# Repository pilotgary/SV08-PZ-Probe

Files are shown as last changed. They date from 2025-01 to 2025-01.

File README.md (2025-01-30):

# SV08-PZ-Probe
E3D Revo PZ-Probe for the Sovol SV08

## Project Aims
1. To swap the supplied hot end and Z probe for the E3D Revo PZ-Probe.
2. To use as many of the existing parts as possible.
3. To work with the Sovol branch of Klipper.
4. 3D printed parts should not require support.

> [!IMPORTANT]
> Full details of the PZ probe can be found on the E3D support page at https://e3d-online.com/pages/e3d-support-pz-probe
> Please read these instruction thoroughly before proceeding. 

## New 3D printed parts 
The new 3d printed parts can be found in the STEP directory.  As most modern slicers can open STEP files directly this is the preferred format for this project.  Premade 3MF files for the Bambu Labs A1 mini and STL files are available in the relevant folders.

The parts should be orientated correctly on import as shown below. All parts have been designed so that support is not required, provided your printer can cope with small bridges.

### Print Orientation
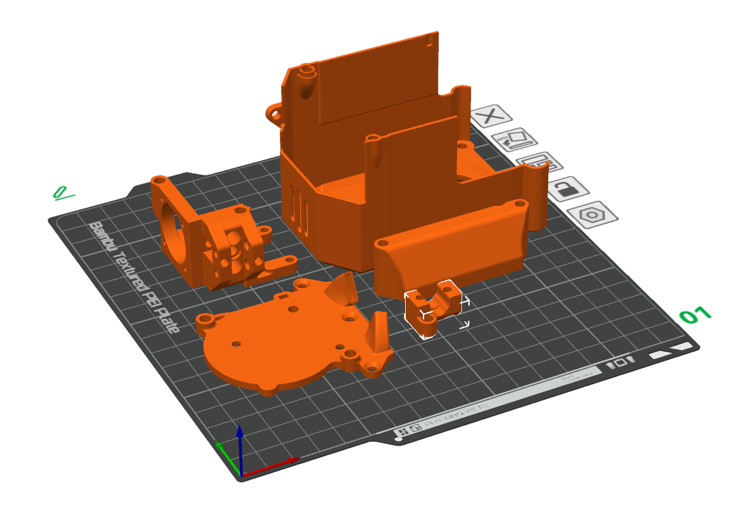
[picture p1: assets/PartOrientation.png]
Part orientation


The prototype was printed in PETG on a Bambu Labs A1 mini, 0.16mm layer height, 3 wall loops, 100% infill.  If your Sovol SV08 has an enclosure or you plan on printing high temperature filamanets, ASA or ABS would be preferred.

## Printed Part Preparation

### Heat set inserts

The parts are designed around M3 x 6mm unflanged inserts, except for the upper two on the main mount, that should be M3 x 5mm.  If preferred, 5mm long inserts can be used in all locations. Alternatively, 6mm inserts can be used everywhere, if you don't mind them sticking out a little from the main mount.  

All inserts should sit level or below the face of insertion.  Any plastic the bulges up should be removed, so that parts fir together without gaps.

#### Main Mount

The main mount upper inserts need to be aligned with the inside of the mounting slot for maximum strength and ease of assembly.  See the image below.

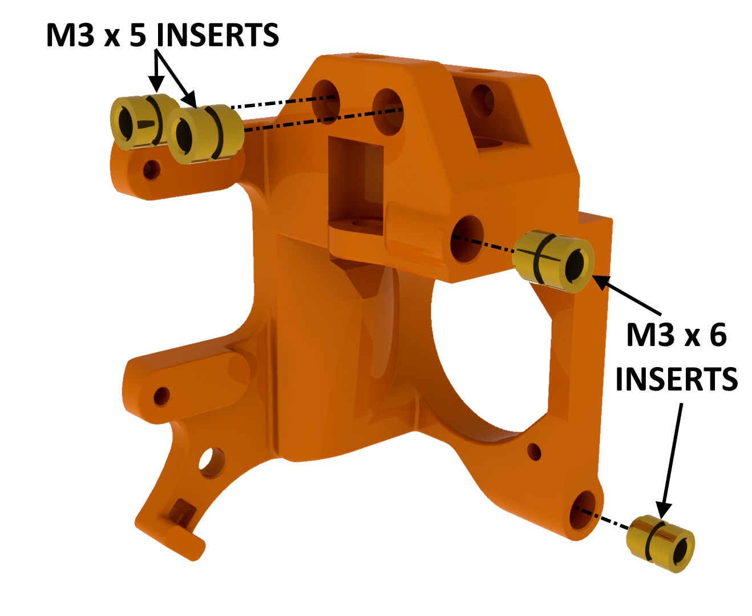
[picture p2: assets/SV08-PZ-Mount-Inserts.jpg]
SV08-PZ-Mount-Inserts
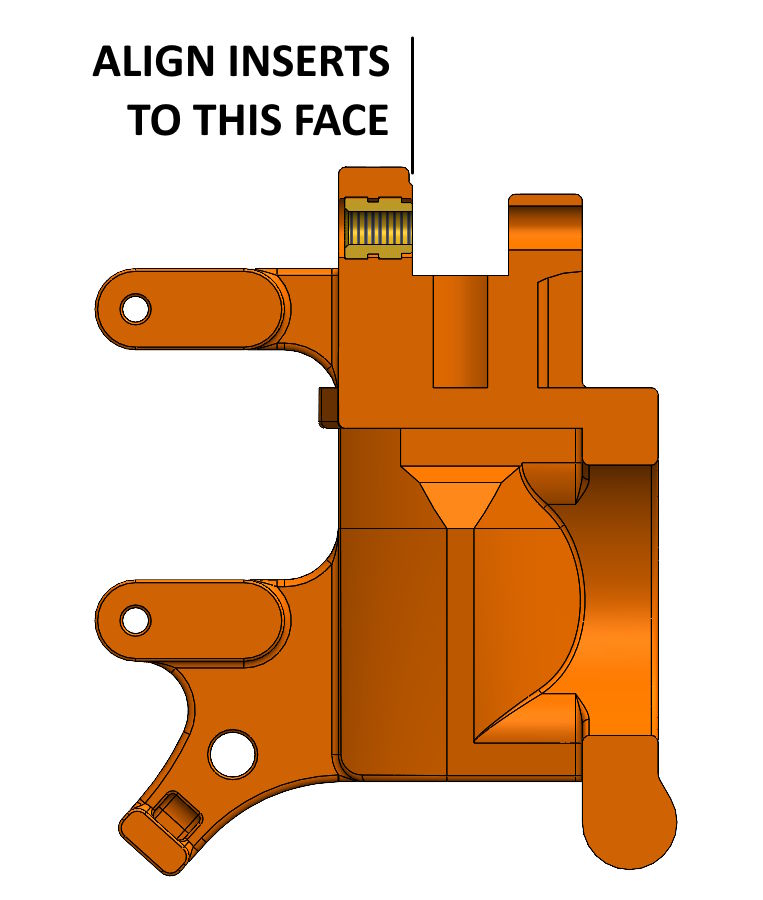
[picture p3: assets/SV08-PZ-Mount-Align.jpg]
SV08-PZ-Mount-Align
 

#### Fan mount with nozzles

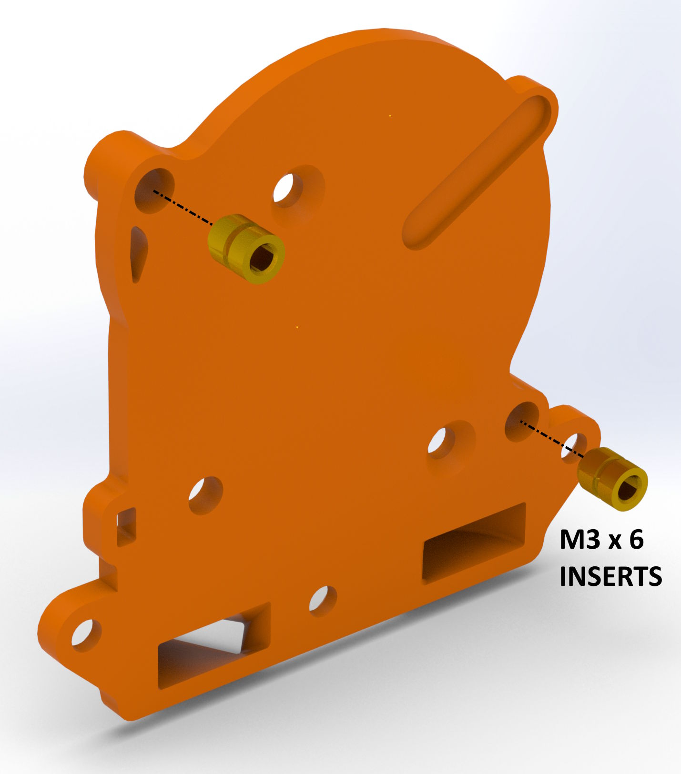
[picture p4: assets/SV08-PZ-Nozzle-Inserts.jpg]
SV08-PZ-Nozzle-Inserts


#### Fan mount interface

Make sure the inserts sit below the mating face and remove any plastic preventing the mating face from sitting flat, to ensure an airtight seal with the nozzles.

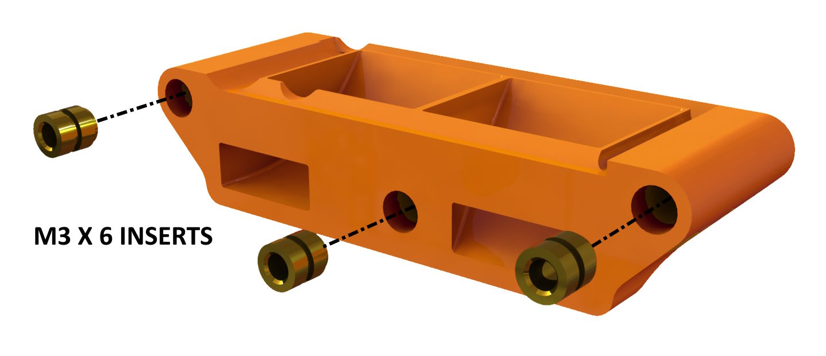
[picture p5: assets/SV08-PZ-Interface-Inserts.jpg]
SV08-PZ-Interface-Inserts


#### Cable clamp

The cable clamp uses a sacrificial layer to support the counterbored screw holes.  This will need to be drilled through.

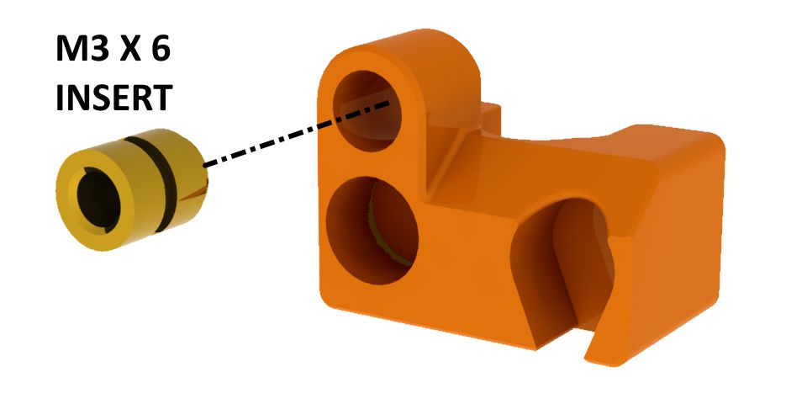
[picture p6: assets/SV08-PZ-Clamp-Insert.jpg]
SV08-PZ-Clamp-Insert
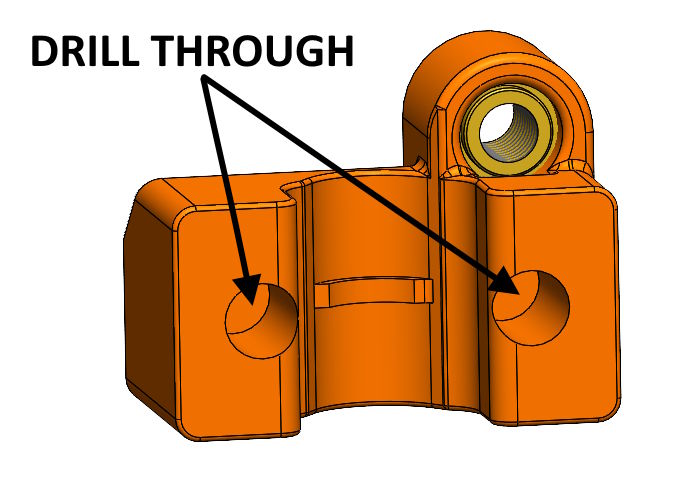
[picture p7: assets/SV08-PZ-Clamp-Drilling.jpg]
SV08-PZ-Clamp-Drilling
  

### Magnets

This design uses 4mm diameter x 3mm long neodium magnets.  I used these ones https://www.amazon.co.uk/dp/B0C81HTXTV

It is important to ensure that the magnets are inserted the correct way round.  The easiest way to ensure this is to snap the magnet to an already mounted one on the tool head and mark the non-contact face with a permanent marker.  The marked face goes at the bottom of the hole on the cover. With care, for some of the magnets, it is possible to push the mounting hole over the magnet while it is snapped in place.

#### Cover

Try to keep all the magnets orientated the same way.

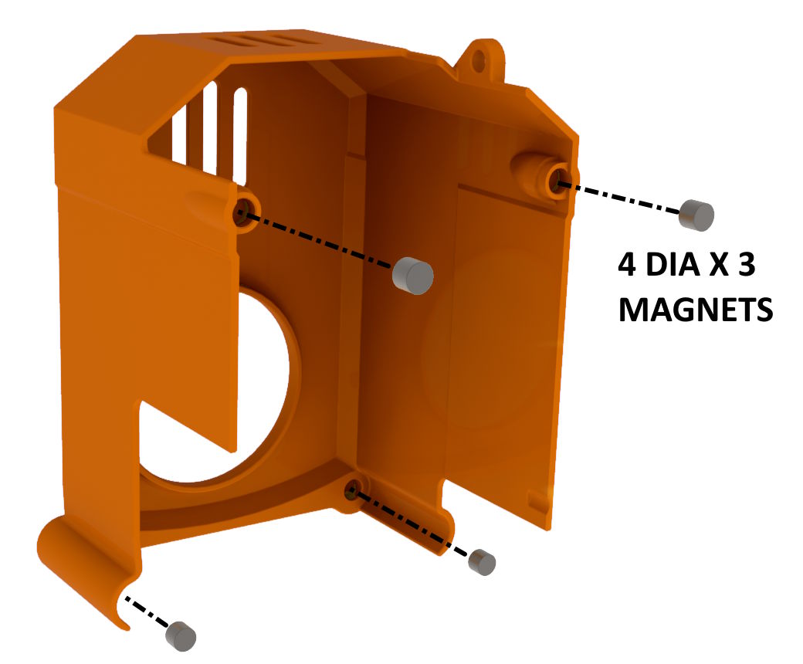
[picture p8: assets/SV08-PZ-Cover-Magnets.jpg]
SV08-PZ-Cover-Magnets


#### Fan mount interface

Snap a magnets to each of the lower pair in the cover.  Slide the interface into the cover and press the two parts together.  Once the magnets are partially seated in the fan interface it can be removed and pressed against a flat surface to fully seat them.

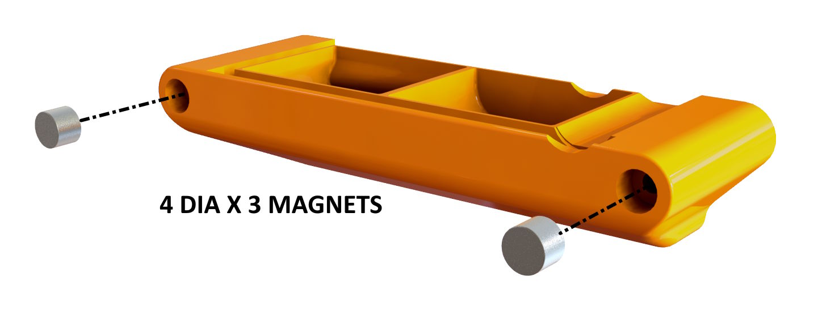
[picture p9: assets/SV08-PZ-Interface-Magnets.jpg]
SV08-PZ-Interface-Magnets


## Stripping the exiting toolhead

1. Home the printer and raise the gantry above 250mm for ease of access with the head front and centre.
   
2. Disconnect the large fan and remove it from the cover.

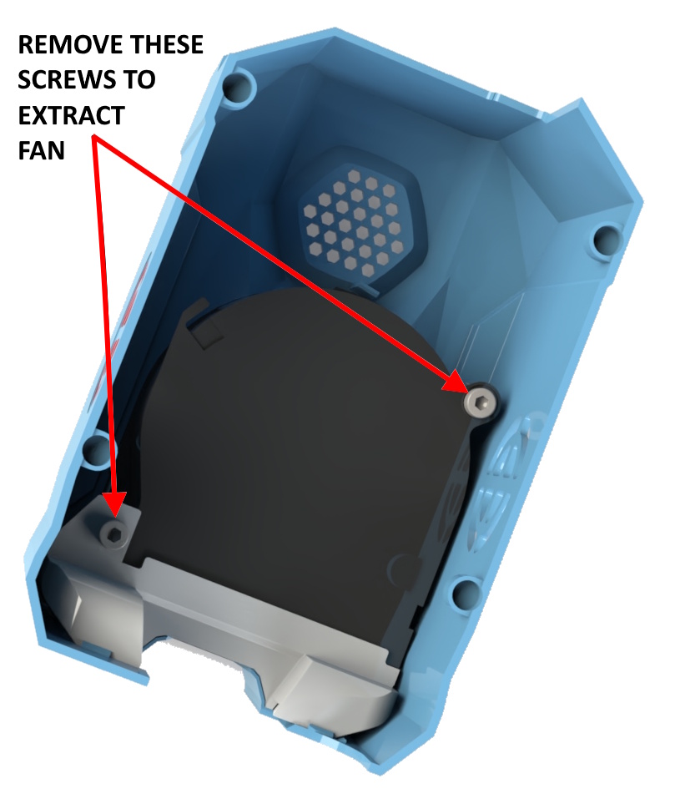
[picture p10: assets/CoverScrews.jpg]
Cover screws
    
    
3. Remove the standard nozzle and heatsink assembly. Clicking on the image below will take you to the relevant Sovol video:
   
   Nozzle change video (http://www.youtube.com/watch?v=bAOVA6bL-Jw)
   
4. Remove the small fan from the heatsink.  Keep the screws.
   
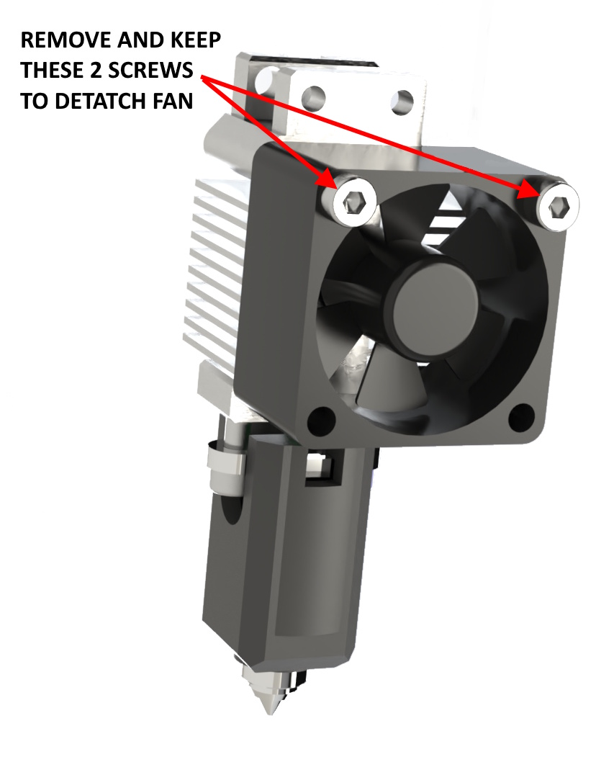
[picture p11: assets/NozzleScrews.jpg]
Nozzle screws
   
   
5. Unscrew the Z-Probe and disconnect the cable. Remove the cable clamp. You can optionally disconnect the power and usb connections for clearer access.
   
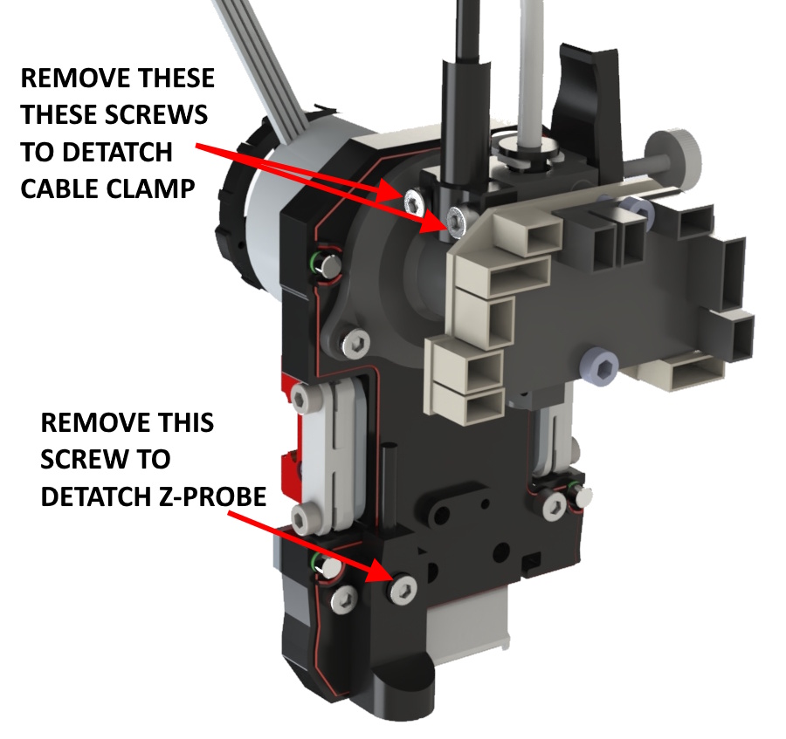
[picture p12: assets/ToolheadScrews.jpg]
Toolhead screws
   

## PZ-Probe Assembly

Align the coldside on the mount so that the cable points away from the fan ring and assemble using M3x6 buttonhead screws.  The two side screws are placed in their cut-outs and the hex driver engages in their heads through the holes in the top.

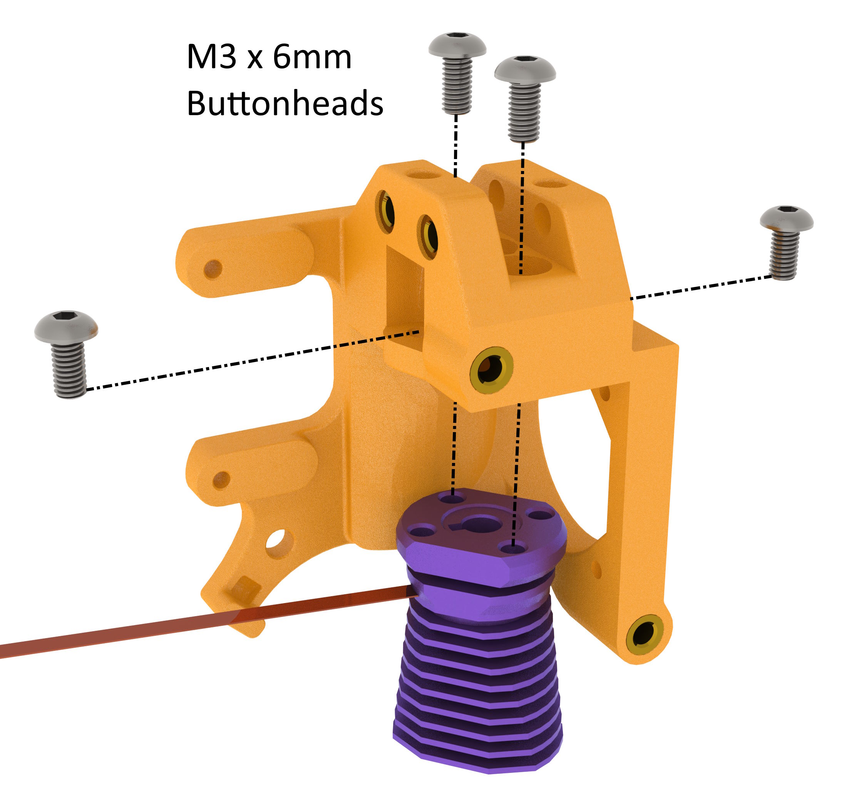
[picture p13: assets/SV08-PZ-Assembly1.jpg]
SV08-PZ-Assembly1
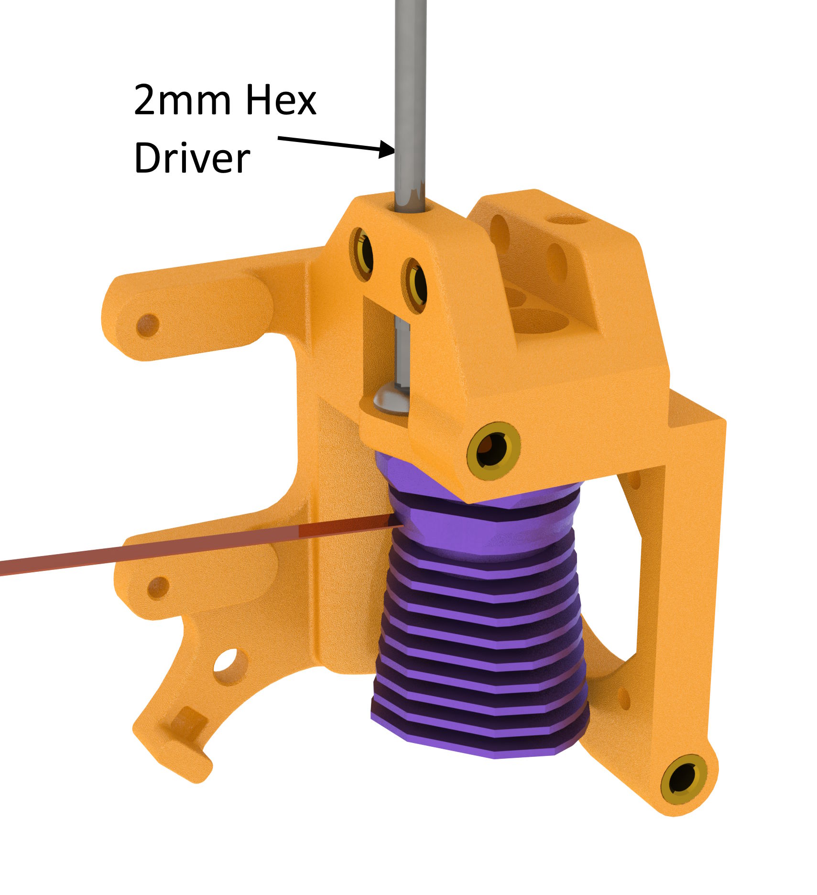
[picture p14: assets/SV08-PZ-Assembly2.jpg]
SV08-PZ-Assembly2
 

Mount the PZ-probe board in place using the M2 capheads supplied with the board.  These screws will cut their own threads in the mount.

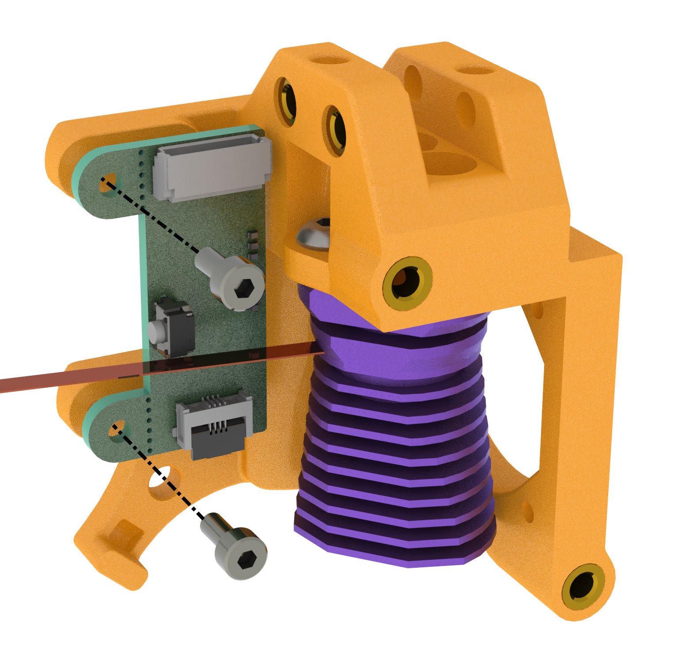
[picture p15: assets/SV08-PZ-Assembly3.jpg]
SV08-PZ-Assembly3


Loop the ribbon cable around and connect tto the pz-probe board.  Use a small zip tie to hold it in place.

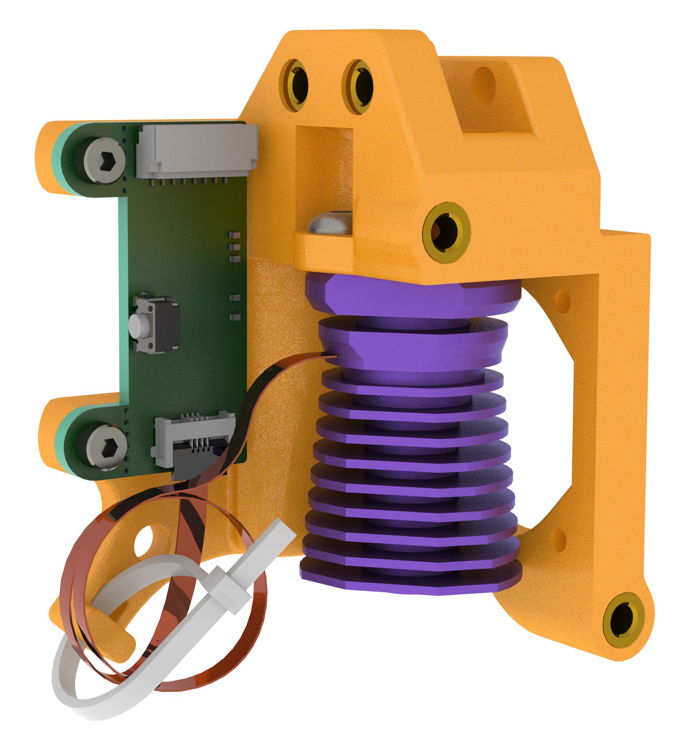
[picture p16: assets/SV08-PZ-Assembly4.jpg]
SV08-PZ-Assembly4
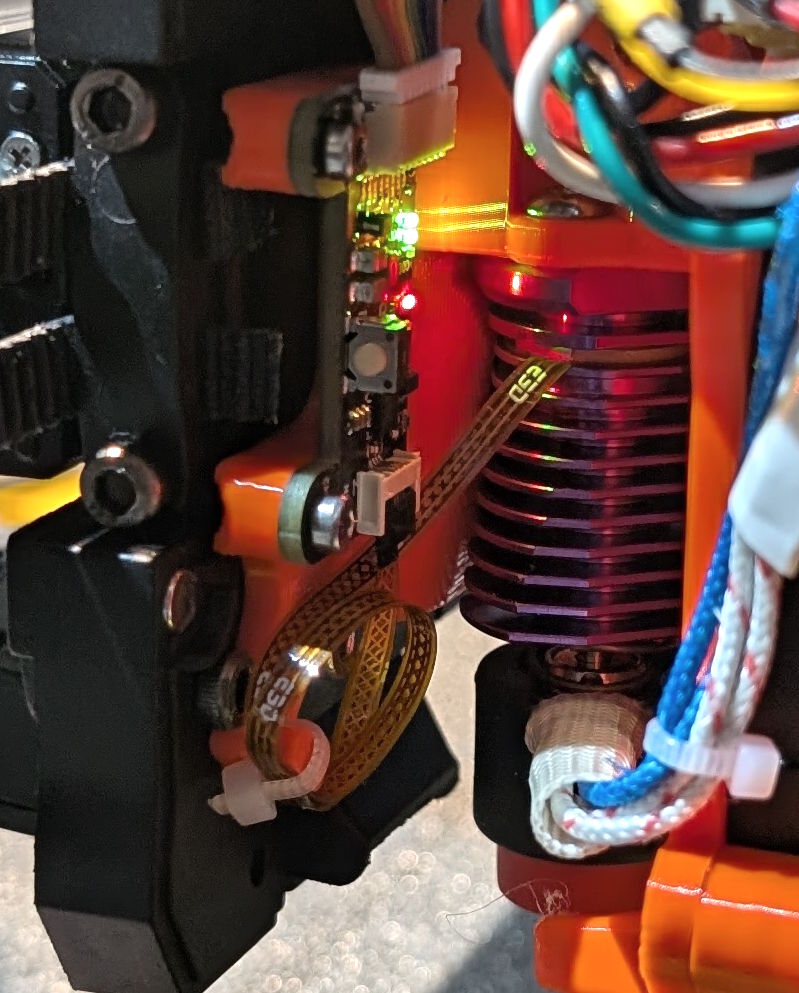
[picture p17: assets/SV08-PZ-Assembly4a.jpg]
SV08-PZ-Assembly4a
 

Using the original 2 screws attach the cold end cooling fan.  4 holes are available but only two are needed.  The screws will cut their own thead.

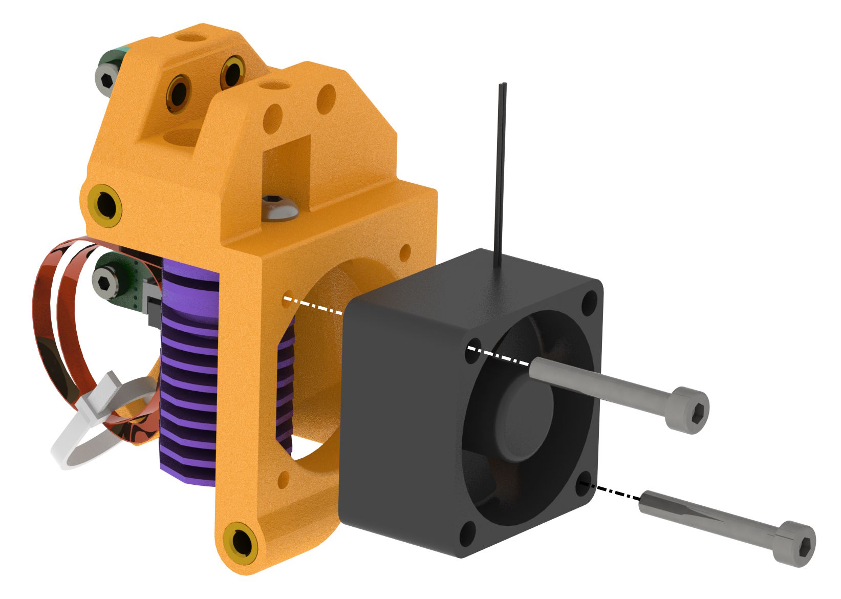
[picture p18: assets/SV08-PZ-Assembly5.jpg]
SV08-PZ-Assembly5


The PZ-Probe comes with a short length of bowden tube. Cut this to 33.5mm, and insert through the mount until it bottoms in the heatsink.  

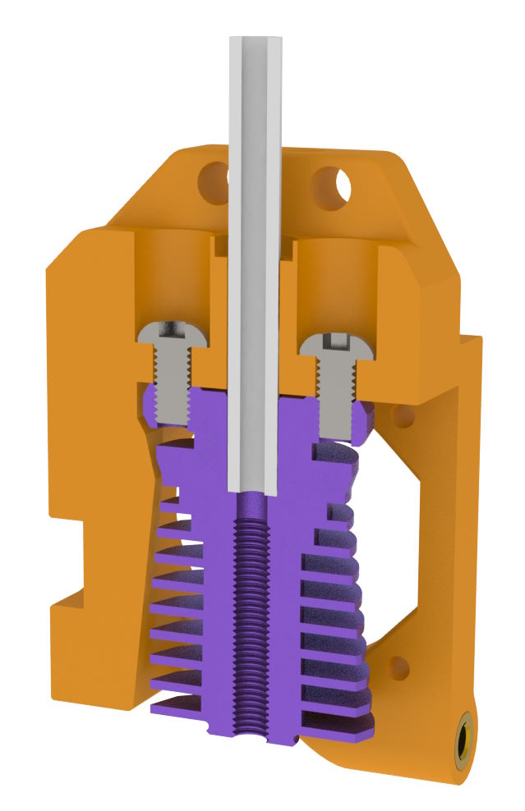
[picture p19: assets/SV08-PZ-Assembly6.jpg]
SV08-PZ-Assembly6


Insert the bowden tube into the toolhead as shown below and push up.  The mount will snap over the original heatsink mount. If the mount doesn't seat completely, trim a small amount off of the bowden tube and try again. 

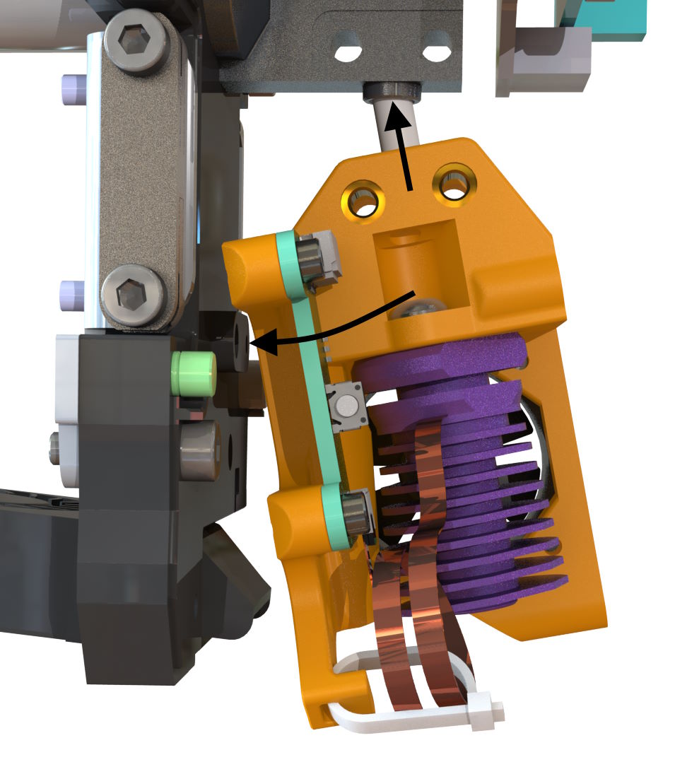
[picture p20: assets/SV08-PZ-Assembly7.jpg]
SV08-PZ-Assembly7
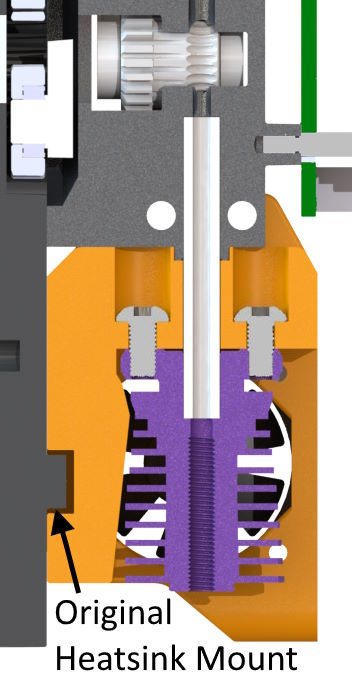
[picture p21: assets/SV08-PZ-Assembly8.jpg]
SV08-PZ-Assembly8
 

Use two M3x20 and one M3x8 screws to secure the mount.  The screws enter from the opposite side compared to the original heatsink.

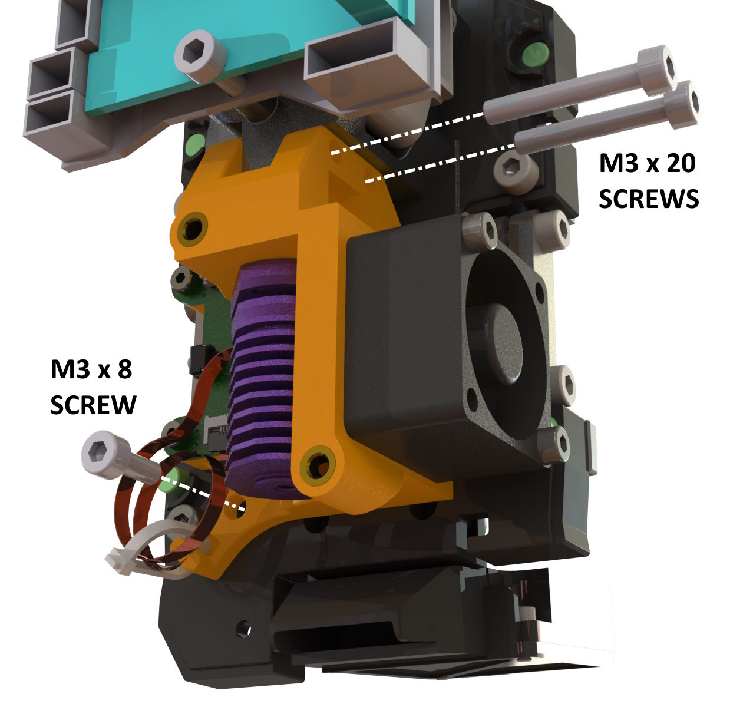
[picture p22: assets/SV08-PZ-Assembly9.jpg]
SV08-PZ-Assembly9


Combine the part cooling fan interface and nozzle items together with three M3x8 countersunk screws

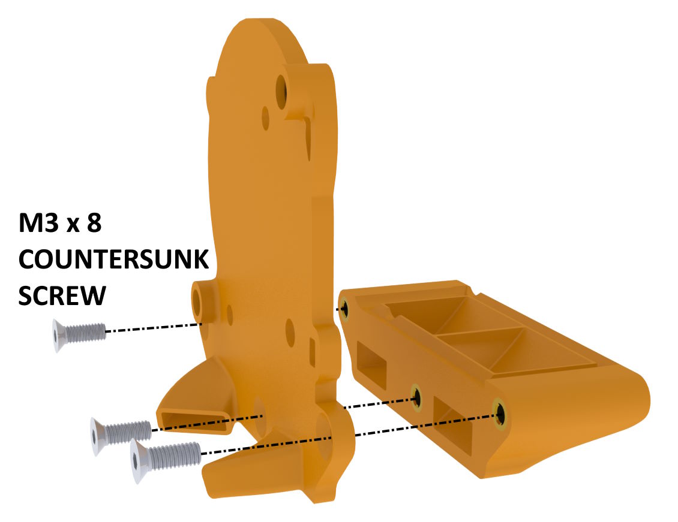
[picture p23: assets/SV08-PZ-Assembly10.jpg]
SV08-PZ-Assembly10


Fix this to the main mount with two M3x8 countersunk screws.  The next stage is the wiring and it's handy to have the fan mount in place to determine the wire lengths.

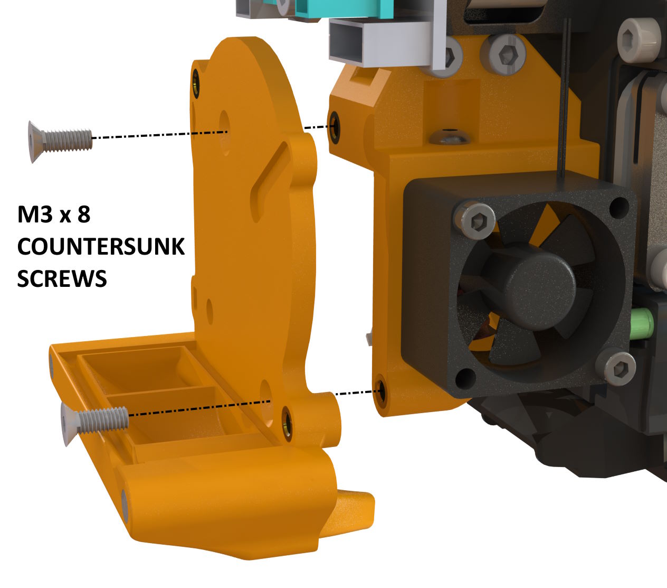
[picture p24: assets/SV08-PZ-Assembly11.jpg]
SV08-PZ-Assembly11


Slot the 5020 fan into the interface and fix with M3x25 screws and washers.  The washers help protect the fan case from splitting from the screw heads. 

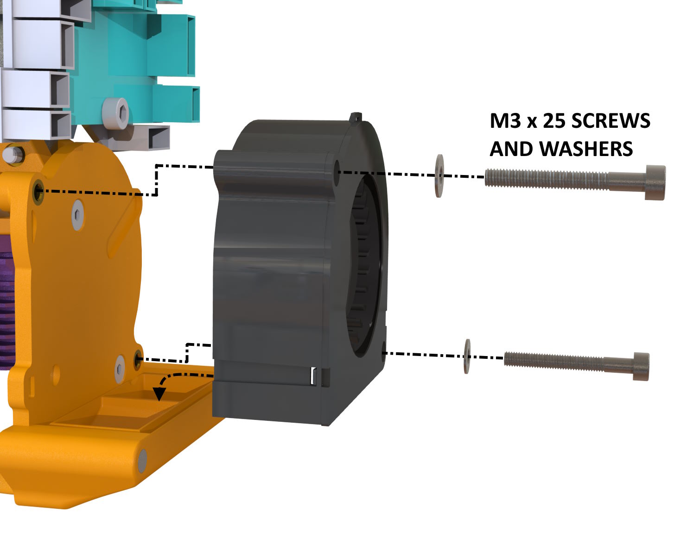
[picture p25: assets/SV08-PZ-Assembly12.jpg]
SV08-PZ-Assembly12


The new screw clamp can be fitted at this stage with M3x12 screws or left until after the wiring is completed.

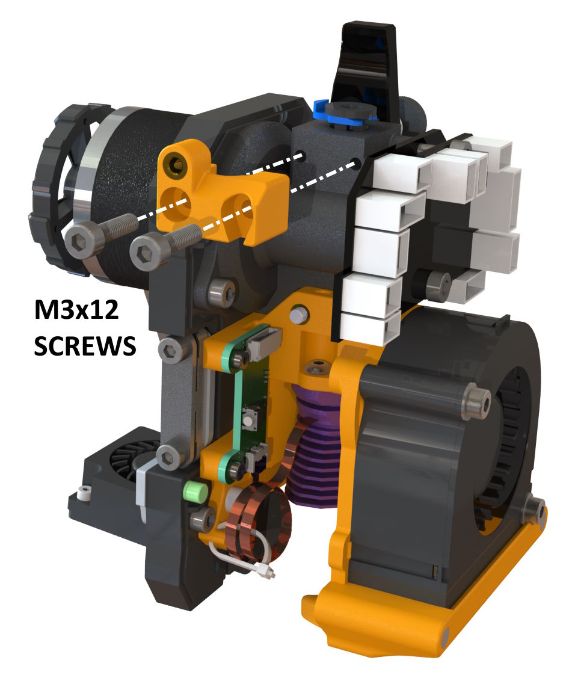
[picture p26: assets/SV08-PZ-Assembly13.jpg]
SV08-PZ-Assembly13


Test fit the cover to ensure the magnets snap together. An M3x8 screw can be used to permanently fix the cover.

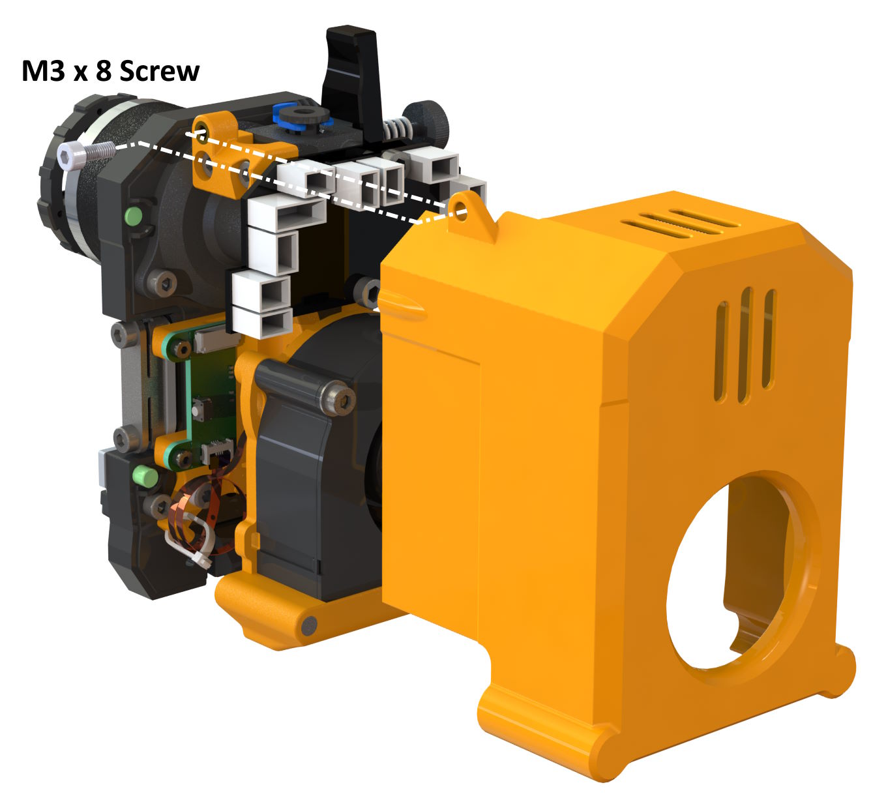
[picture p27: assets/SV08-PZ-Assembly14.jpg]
SV08-PZ-Assembly14


This completes the mechanical assembly.

## PZ-Probe Wiring

> [!CAUTION]
> The supplied Z-probe on the Sovol SV08 uses 24V power.  **DO NOT** connect the PZ-probe board to the the same pin as this will burn out the PZ-probe control board.  Use the 5V pin on the lower right UART per the image below. 

The Sovol SV08 uses a variety of connectors. While the existing probe connector can be harvested, a second one is required for 5V power taken from the spare UART. Both connectors are JST-GH plugs with 1.25mm pin spacing: 5 pin for the probe and 4 pin for the UART. I used this kit from Amazon https://www.amazon.co.uk/gp/product/B0CW2NKVL7

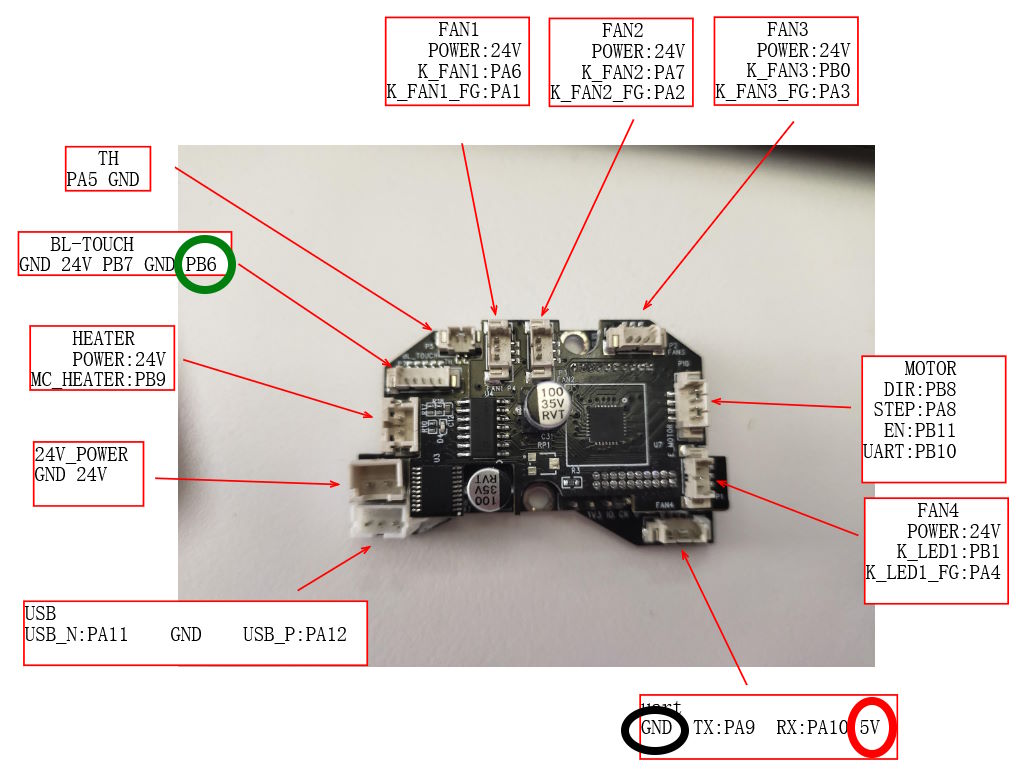
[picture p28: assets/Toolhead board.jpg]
Toolhead Board


Three ground pins are available. I used the one on the UART to keep the wiring neat for the later addition of an X-axis limit microswitch.

> [!IMPORTANT]
> Full details of the PZ probe wiring and programming can be found on the E3D support page at https://e3d-online.com/pages/e3d-support-pz-probe

The wiring harness for the PZ-probe on the SV08 is shown below, along with the colour key for the wiring.  The blue, purple and grey wires were not used, but were terminated with a Dupont connector to keep things tidy.  

A second ground wire was spliced in for the connection to an USB-TTL or FTDI for programming the PZ-probe. This ground along with the RX and TX lines terminate in at a 3 pin Dupont connector.  

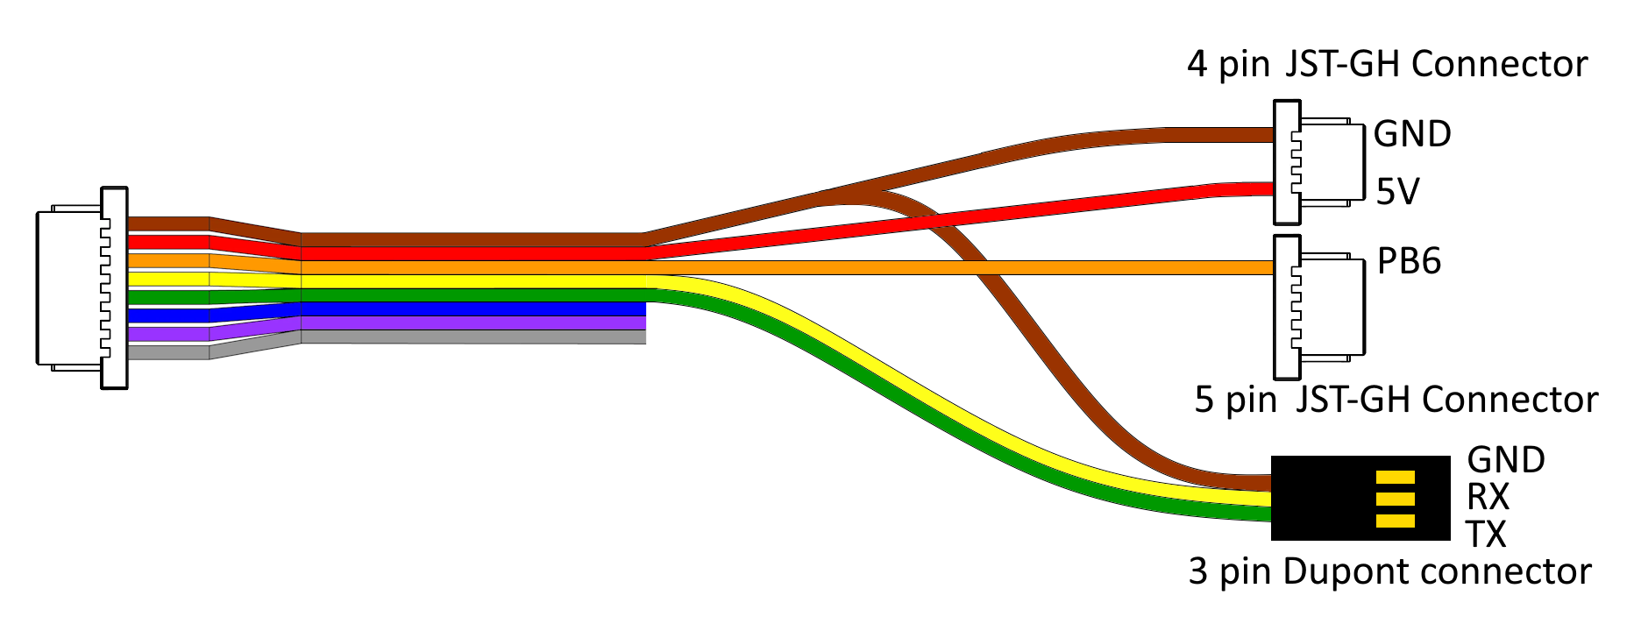
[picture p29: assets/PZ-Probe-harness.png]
PZ-Probe-harness


```
Wire colour and their function:
    Brown - GND (0V)
    Red - PWR (3.3V-5V)
    Orange - Trigger
    Yellow - RX
    Green - TX
    Blue - UPDI
    Purple - SCL
    Grey - SDA
```

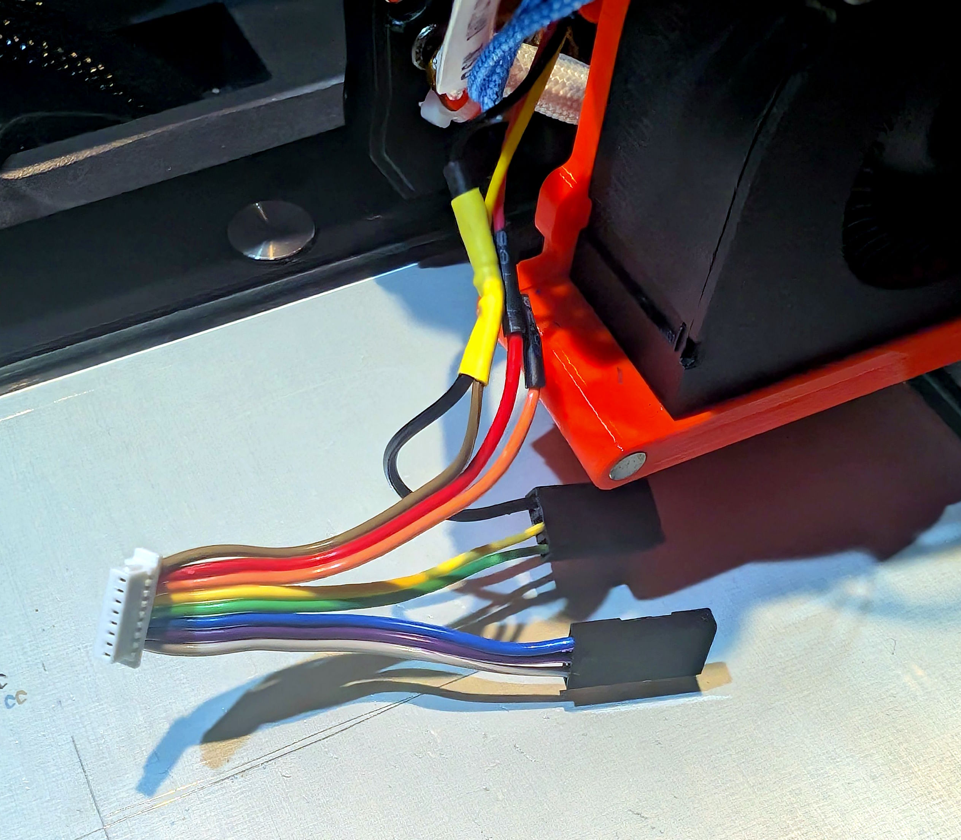
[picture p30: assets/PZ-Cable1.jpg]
PZ-Cable1


## Hotend Wiring

If you don't have the right connectors on hand, harvest the ones from the Sovol heater and thermister.  Cut them off keeping 15mm to 20mm of wire tails attached.  Fit the E3D Revo hotend to the heatsink. The Revo has Molex connectors fitted and comes with extension cables.  For the initial setup I used the extension cables, but later removed them, cutting off the Molex, and soldering the cables to the toolhead connector tails, making sure there was a little slack in the cables once connected.

For mine I had a new plug for the heater and re-used the one from the original thermistor.  I also used some liquid insulation tape for strain relief. 

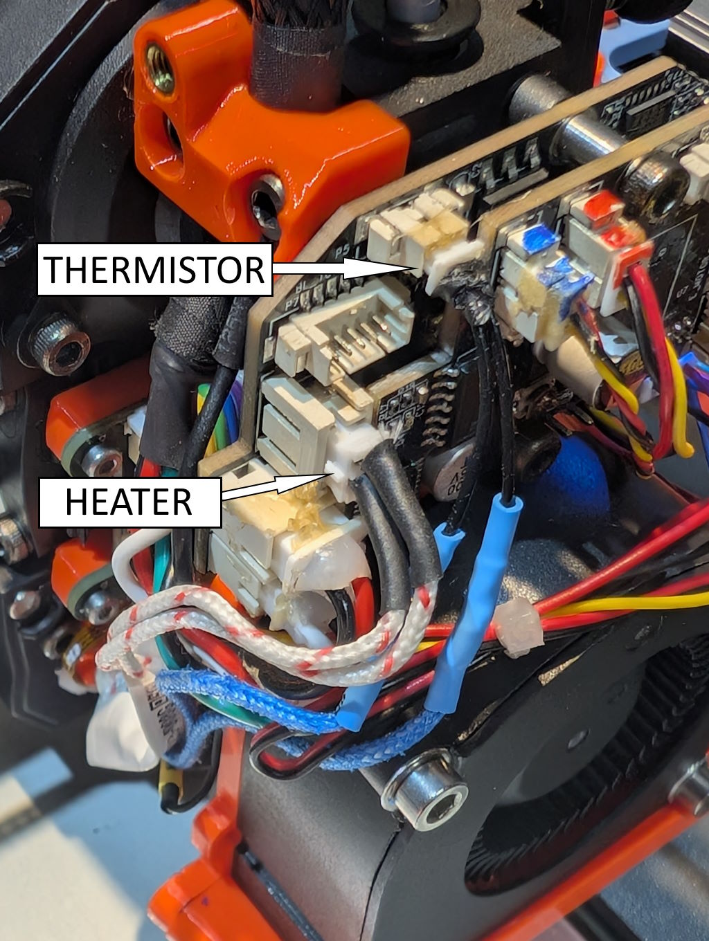
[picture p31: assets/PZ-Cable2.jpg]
PZ-Cable2


## Initial Testing

1. Check the wiring, making sure the PZ-probe power lead goes to the 5V pin on the UART.
2. Power on the printer. If all is good the PZ-probe board should have an illumated red LED.
3. Gently tap the end of the nozzle with metal ruler or screwdriver.  You should see an orange LED flash on the PZ-probe board. 

## Printer Configuration

The configuration below is based on the E3D document at https://e3d-online.com/pages/e3d-support-pz-probe in the Setup Guide->Firmware - Klipper section.

It recommends:
>During probing, reduce the current as much as possible without causing a stall. A good starting point is 40%, but lowering it further, if possible, will reduce the risk of damaging your bed. We have set our probing speed to 5 mm/s.

### Editing printer.cfg

1. Open Mainsail in the web browser, go to the machine page and edit the printer.cfg file.

2. Find the [probe] section and comment out the existing entries with a # at the start of the line, so it looks similar to the below.  Your values may look different depending on what customization you have done to the default settings.
```
#[probe]
#pin: extra_mcu:PB6    
#x_offset: -17                  
#y_offset: 10             
#z_offset : 0
#speed: 10  #  was 15.0
#speed: 10.0  # was 5.0
#samples: 3  # was 2
#sample_retract_dist: 5.0 # was 2.0
#lift_speed: 25 # was 50
#samples_result: median # was average
#samples_tolerance: 0.0125 # was 0.016
#samples_tolerance_retries: 10 # was 2
```

4. Paste in the following text

```
#####################################################################
#   Probe
#####################################################################

[probe] ## Other parameters in config.cfg
pin: !extra_mcu:PB6
x_offset: 0.001
y_offset: 0.001
speed: 5.0 #   Speed (in mm/s) of the Z axis when probing. The default is 5mm/s.
samples: 2
sample_retract_dist: 3.0
samples_tolerance_retries: 1
lift_speed: 10
activate_gcode:
    G4 P200 ;Wait 200ms
    SET_TMC_CURRENT STEPPER=stepper_z CURRENT=0.4
    SET_TMC_CURRENT STEPPER=stepper_z1 CURRENT=0.4
    SET_TMC_CURRENT STEPPER=stepper_z2 CURRENT=0.4
    SET_TMC_CURRENT STEPPER=stepper_z3 CURRENT=0.4
deactivate_gcode:
    {% set run_current = printer.configfile.config['tmc2209 stepper_z'].run_current | float %}
    SET_TMC_CURRENT STEPPER=stepper_z CURRENT={run_current}
    SET_TMC_CURRENT STEPPER=stepper_z1 CURRENT={run_current}
    SET_TMC_CURRENT STEPPER=stepper_z2 CURRENT={run_current}
    SET_TMC_CURRENT STEPPER=stepper_z3 CURRENT={run_current}
```

> [!NOTE]
> The Sovol Klipper build does not allow the x_offset and y_offset values to be zero. Setting them to 1 micron (0.001mm) works well enough.

4. Save and reboot

## Further Testing

> [!IMPORTANT]
> Revo hot ends can be bent if dragged across the bed.  Make sure that gantry lifts before any movements and turn off immediately if it contacts the bed.  Don't run the nozzle cleaning macro at this stage.

1. Use the web interface to home the Z axis.
   - If there is a short movement and the descent stops, the PZ-probe is probably too sensitive.  Press the button on the PZ-probe board to change the sensitivity threshold from 5 to 10.  One of the green LEDs should be lit.  Try homing again. The threshold can be further reduced to 15 with another button press. See the troubleshooting section on the E3D support page (https://e3d-online.com/pages/e3d-support-pz-probe) 
   - Once the gantry starts to descend, tap the nozzle with a tool.  The gantry should stop descending and lift slightly and then descend again. If the descent doesn't stop, power off the printer and check the wiring.  Power the printer back on and check the configuration.  If the first tap was detected, tap the nozzle again and descent should stop.

2. Press **Home All**.  If the printer completes the homing cycle all is good. If not, check the E3D PZ-probe troubleshooting section.  On my machine, I needed to set the threshold to 18 using a USB-TTL adapter.

## Nozzle cleaning

Using the nozzle for probing, requires it to be clean. Ideally we want to do an initial home all, then clean the nozzle followed by another Z home.   

To be safe, increase the Z distances in the CLEAN_NOZZLE macro (found in Macros.cfg) by 10mm, run the macro and then decrease them in steps until the nozzle contacts with silicone wiper, without dragging or catching. 

Below is a modified version of the CLEAN_NOZZLE macro. Look for the ######## HEIGHT INCREASED ######## comments for the altered lines.

```
[gcode_macro CLEAN_NOZZLE]
gcode:
    {% if printer.toolhead.homed_axes != "xyz" %}
       G28 ; Home all axes if not already homed
    {% endif %}
    G90 ; Set to absolute positioning
    G1 X348 Y0 Z10.3 F9000 ; Move to the cleaning start position (X348, Y0) and set Z to 0.3mm ######## HEIGHT INCREASED - WAS Z0.3 #######
    M117 Nozzle heating...
    M109 S200 ; Wait for the nozzle to heat up to 200°C
    G91 ; Switch to relative positioning
    G1 Z10 F300 ; Raise the nozzle by 10mm at a slow speed ######## HEIGHT UNCHANGED #######
    G90 ; Switch back to absolute positioning
    M106 S255 ; Turn on the fan at full speed
    M104 S130 ; Set the nozzle temperature to 130°C without waiting
    M117 Clean nozzle 
    G1 X315 Y360 F9000 ; Move the nozzle to a new cleaning position at fast speed
    G1 Z10.2 F300 ; Lower the nozzle to 0.2mm above the bed slowly ######## HEIGHT INCREASED - WAS Z0.2 #######
    G1 X352 F4500 ; Sweep the nozzle horizontally along the X-axis at medium speed
    ; Perform multiple passes along X and Y to clean the nozzle
    G1 Y360 X324
    G1 Y360 X345
    G1 Y360 X324
    G1 Y360 X345
    G1 Y360 X324
    G1 Y360 X345
    G1 Y360 X324
    G1 Y360 X345
    G1 Y360 X324
    G1 Y360 X325
    G1 Y356 X324 Z15 ; Slightly lift Z while moving ######## HEIGHT INCREASED - WAS Z5 #######
    G1 Z10.2 ; Lower back to 0.2mm ######## HEIGHT INCREASED - WAS Z0.2#######
    G1 Y360 X324 ; Repeat fine movements for cleaning
    G1 Y357 X326
    G1 Y360 X326
    G1 Y357 X328
    G1 Y360 X330
    G1 Y357 X332
    G1 Y360 X334
    G1 Y357 X336
    G1 Y360 X338
    G1 Y357 X340
    G1 Y360 X324
    G1 Y357 X326
    G1 Y360 X326
    G1 Y357 X328
    G1 Y360 X330
    G1 Y357 X332
    G1 Y360 X334
    G1 Y357 X336
    G1 Y360 X338
    G1 Y357 X340
    G1 Y360 X324
    G1 Y357 X326
    G1 Y360 X326
    G1 Y357 X328
    G1 Y360 X330
    G1 Y357 X332
    G1 Y360 X334
    G1 Y357 X336
    G1 Y360 X338
    M400 ; Wait for all movements to finish
    M117 Clean Finish
    M109 S130 ; Wait for the nozzle to cool down to 130°C
    M107 ; Turn off the fan
    G91 ; Switch to relative positioning
    G1 Z10 F300 ; Raise the nozzle by 10mm to clear the cleaning area ######## HEIGHT UNCHANGED #######
    G90 ; Switch back to absolute positioning
    G28 Z0 ; Home the Z-axis to ensure it's reset
```

## Results

Initial testing has been promising.  I printed a grid of disks, which came out well and suggested a small (+0.05 to +0.1mm) Z offset produced the best first layer.

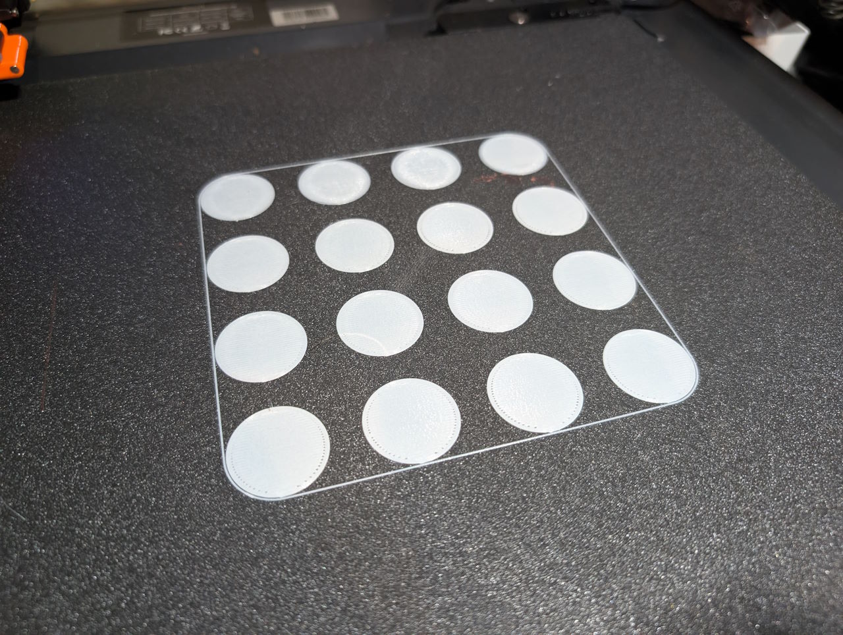
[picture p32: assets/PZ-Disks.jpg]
PZ-Disks


I did a full bed mesh which showed a horrendous amount of curvature (almost 1mm) and probably explains the gouges in the bed when running the automatic Z compensation when the printer was new.  Attempts to adding packing to flatten the bed didn't produce adequate results.  As I had removed the magatic sheet and the PZ-Probe doesn't need a metalic surface, I tried using a 350mm x 350mm x 6mm sheet of glass as the bed. This works well as the hard surface triggers the probe more reliably.

Running the mesh with the glass bed cold, showed it was not as flat as hoped, but better with a range of 0.25mm.  Rotating the glass 90 degrees and repeating the mesh showed that the curvature rotated with the bed, so the probe has to be reading true.   

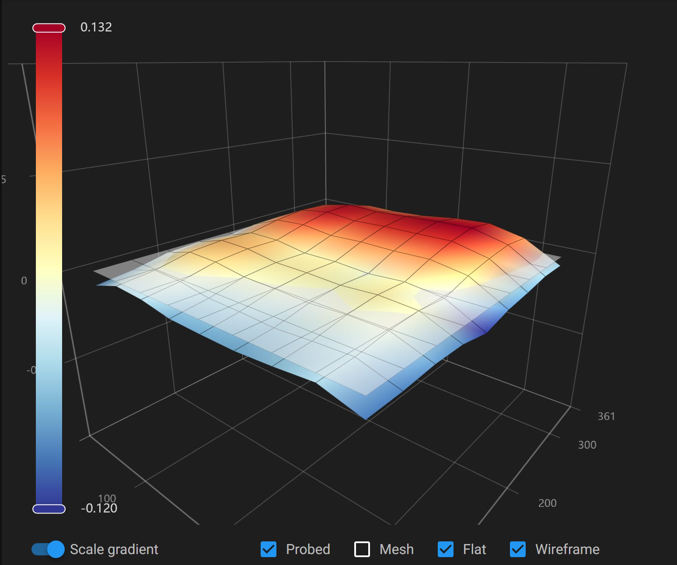
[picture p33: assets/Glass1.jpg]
Glass1
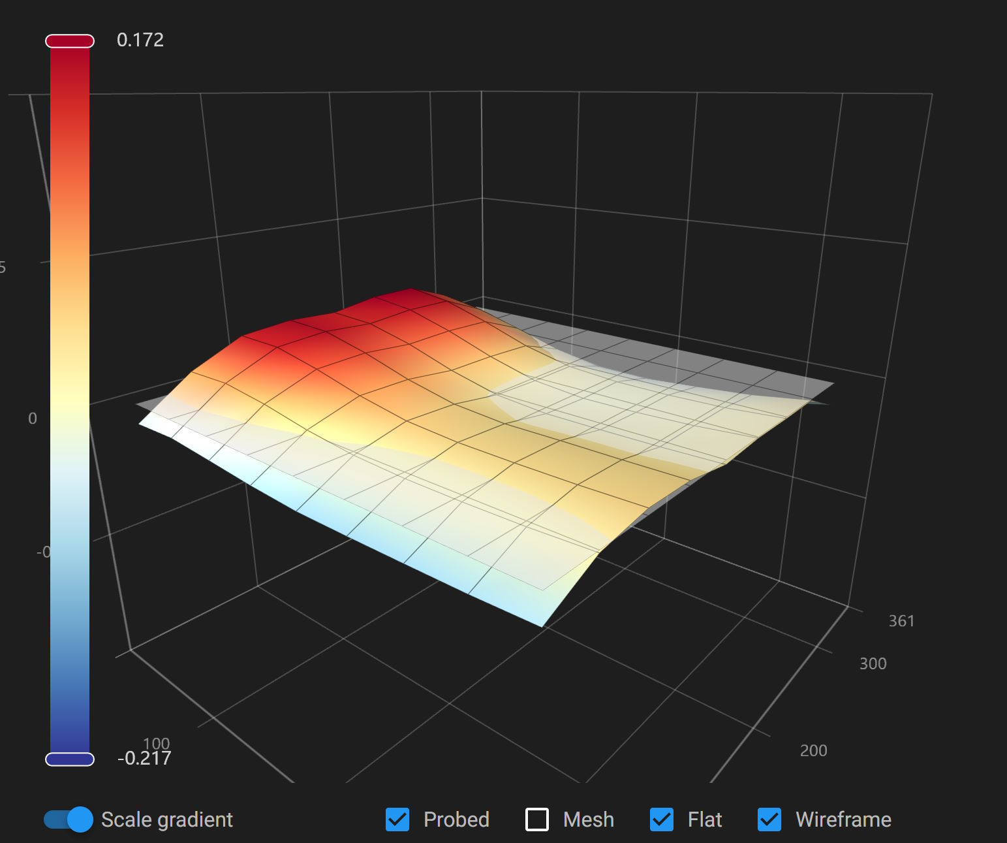
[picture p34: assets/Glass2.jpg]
Glass2
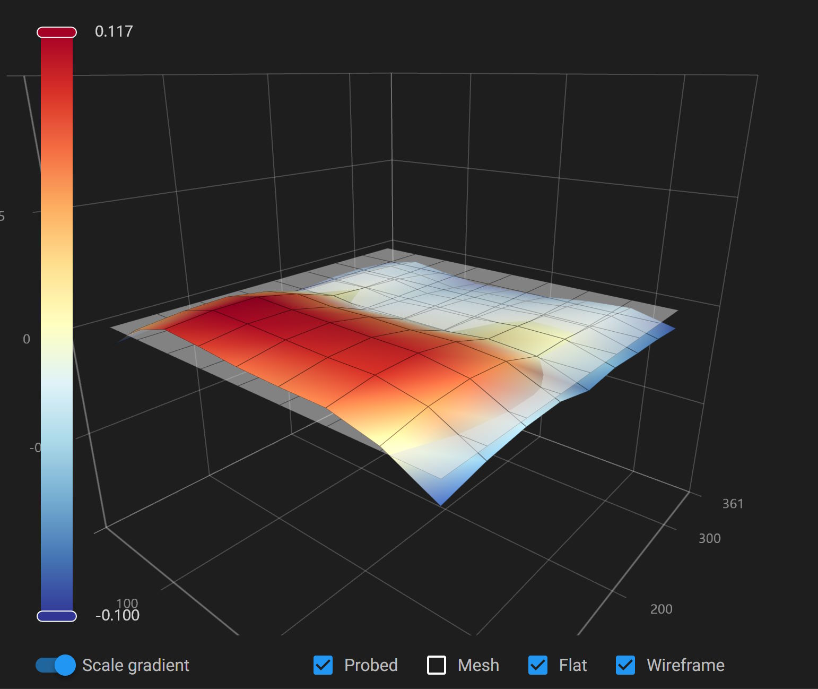
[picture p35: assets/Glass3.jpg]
Glass3
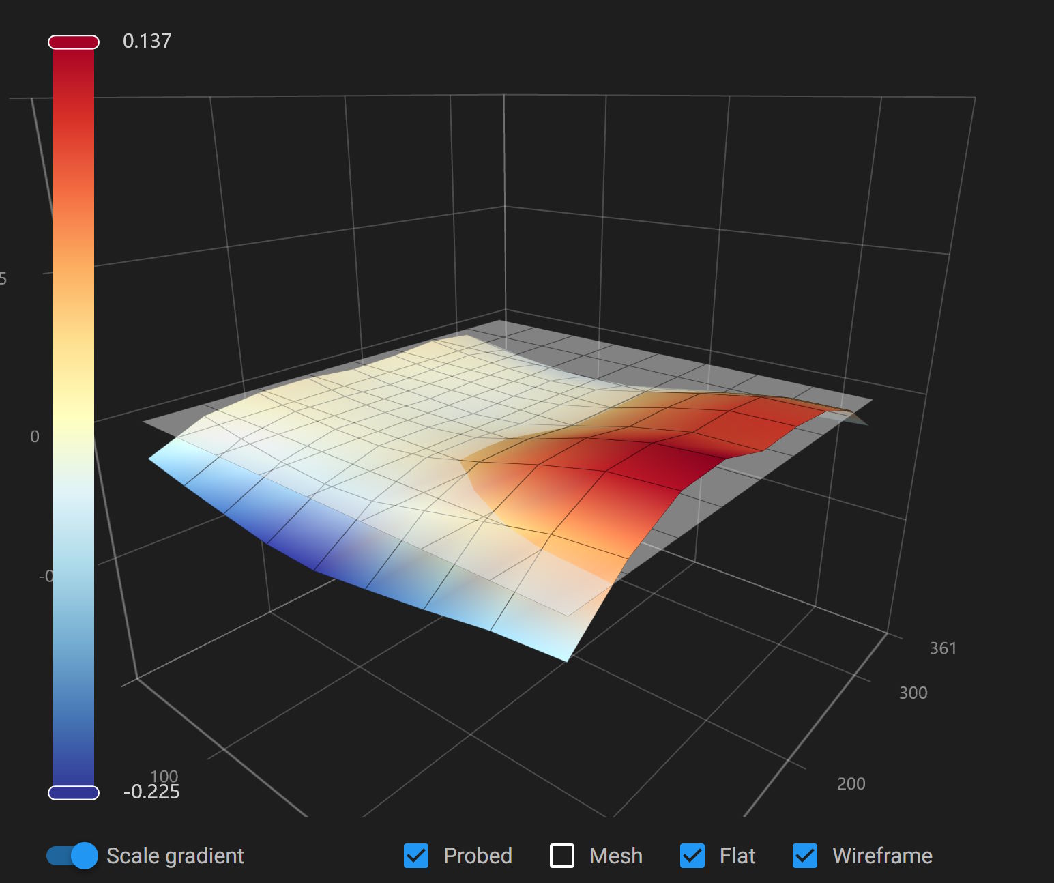
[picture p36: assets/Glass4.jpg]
Glass4
   

## The future

This is still a work in progress with more work required, espcially on the macros.  I also plan to switch the virtual X and Y endstops over to microswitches or optical switches.  I might switch to proper Voron 2.4 heat bed as well.

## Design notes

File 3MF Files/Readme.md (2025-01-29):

# Bambu Labs Slicer Project Files

This folder contains premade project files for the Bambu Labs A1 mini.

The print setttings are 0.16mm layer height, 3 wall loops, 100% infill.

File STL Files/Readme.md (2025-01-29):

# STL files

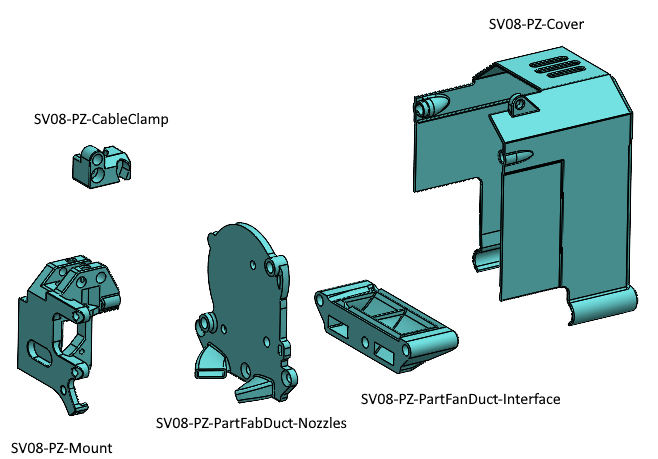
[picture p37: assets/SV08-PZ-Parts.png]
SV08-PZ-Parts


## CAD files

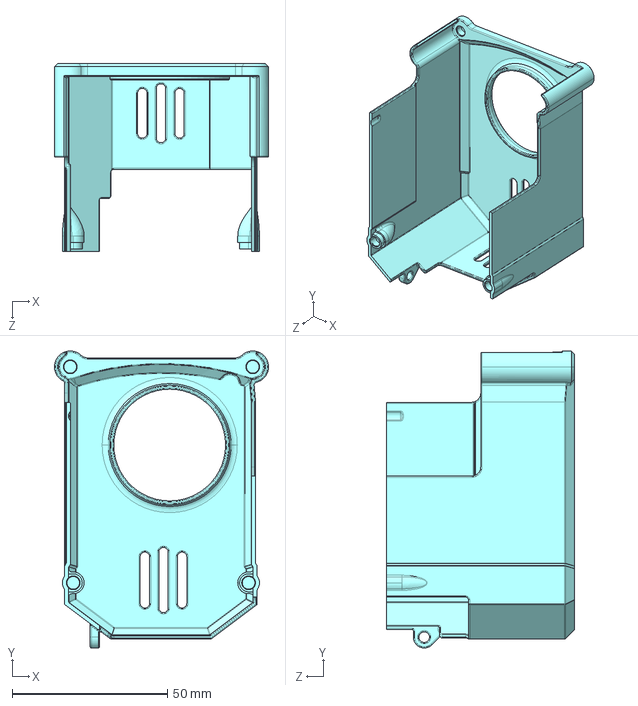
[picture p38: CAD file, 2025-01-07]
STEP Files/SV08-PZ-Cover.STEP
69.0 x 95.7 x 60.5 mm

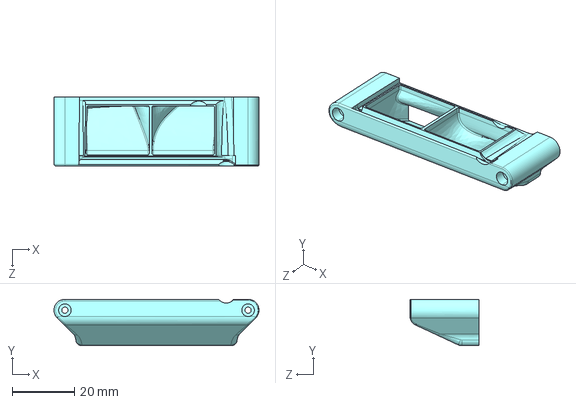
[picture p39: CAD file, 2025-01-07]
STEP Files/SV08-PZ-PartFanDuct-Interface.STEP
65.8 x 14.9 x 22.1 mm

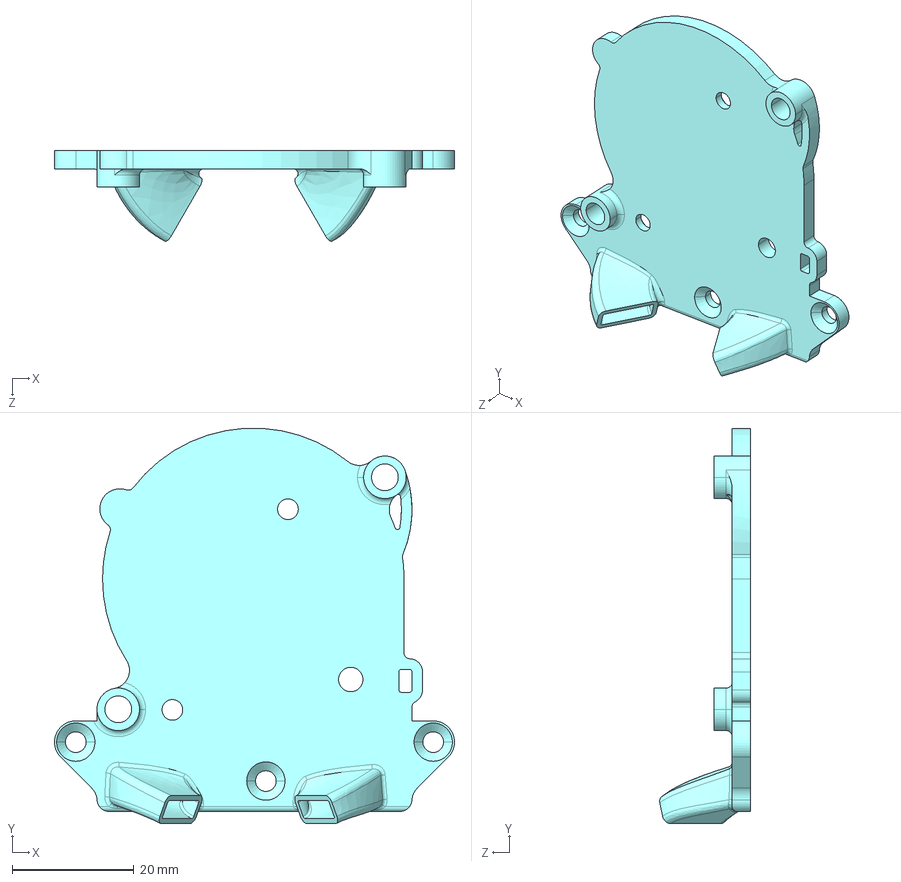
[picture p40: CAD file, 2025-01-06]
STEP Files/SV08-PZ-PartFanDuct-Nozzles.STEP
65.8 x 65.0 x 14.9 mm

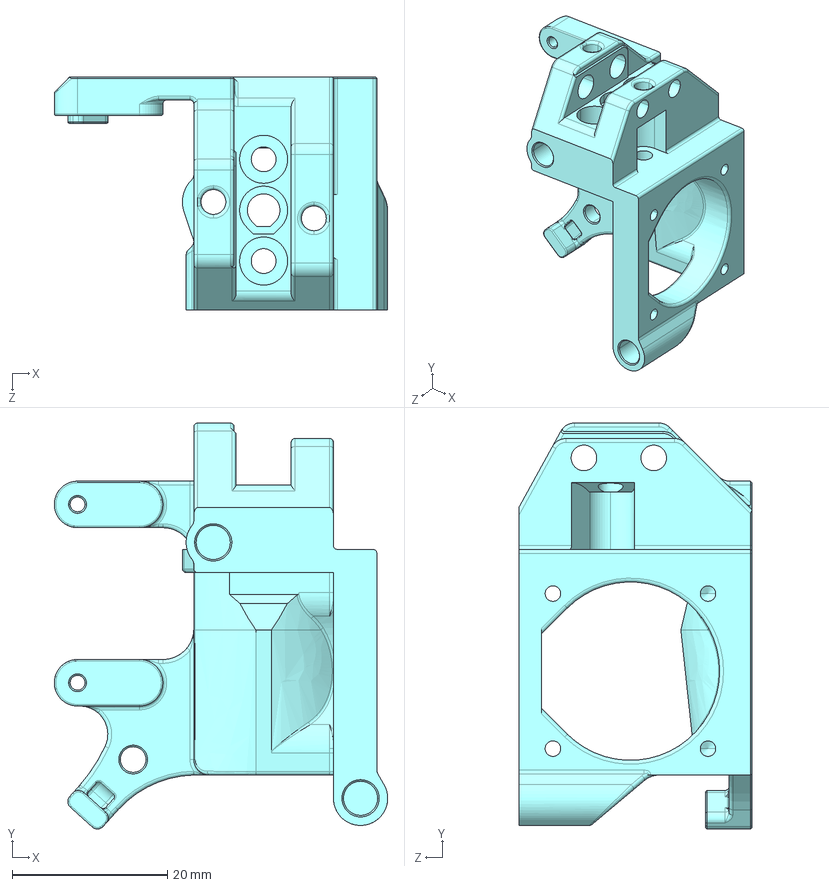
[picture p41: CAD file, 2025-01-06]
STEP Files/SV08-PZ-Mount.STEP
43.0 x 52.4 x 30.1 mm

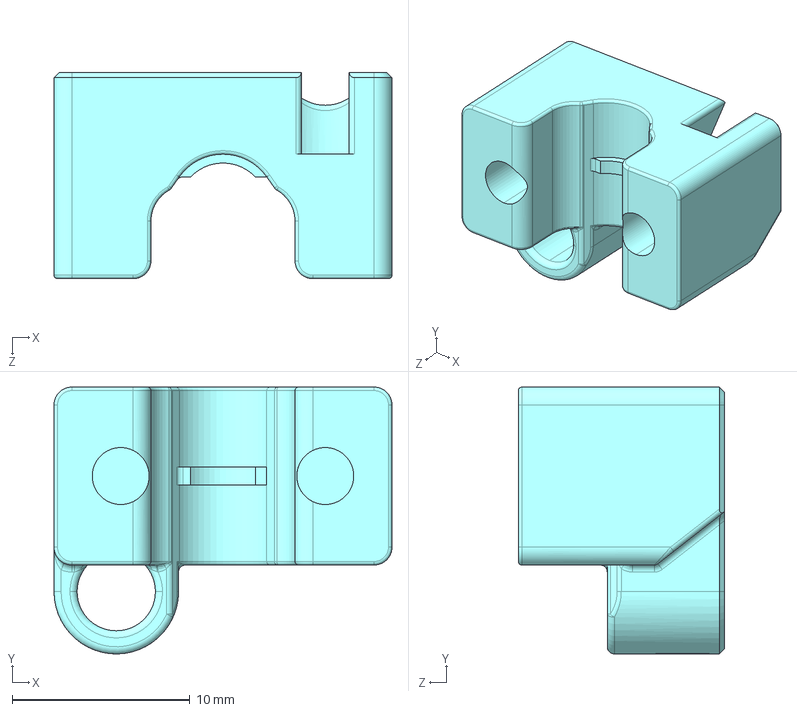
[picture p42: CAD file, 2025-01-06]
STEP Files/SV08-PZ-CableClamp.STEP
19.0 x 15.0 x 11.6 mm

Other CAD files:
3MF Files/SV08-PZ-Cable clamp.3mf
3MF Files/SV08-PZ-Cover.3mf
3MF Files/SV08-PZ-Mount.3mf
3MF Files/SV08-PZ-PartFanDuct-Interface.3mf
3MF Files/SV08-PZ-PartFanDuct-Nozzles.3mf

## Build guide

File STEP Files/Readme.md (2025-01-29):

# STEP Files

SV08-PZ-Parts

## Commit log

2025-01-07 Update README.md
    Add 3d print details
2025-01-07 Add files via upload
    Correct Orientation
    [SV08-PZ-PartFanDuct-Interface.STEP]
2025-01-07 Rename 3mf folder
    [SV08-PZ-Cable clamp.3mf, SV08-PZ-Cover.3mf, SV08-PZ-Mount.3mf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]
2025-01-29 Rename STL dir
